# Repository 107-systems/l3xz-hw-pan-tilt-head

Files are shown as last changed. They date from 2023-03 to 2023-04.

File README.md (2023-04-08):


`l3xz-hw-pan-tilt-head`
=======================


This repository contains the design files for [L3X-Z](https://github.com/107-systems/l3xz)'s pan/tilt color/thermal camera head.

The necessary [ROS](https://docs.ros.org/en/humble/Releases.html)-based driver software for installation on the Raspberry Pi Zero can be found [here](https://github.com/107-systems/l3xz-sw-pan-tilt-head).

<p align="center">
  
</p>

## Overview
_(note that pngs with labels have draw.io diagrams embedded in them and can be edited using draw.io)_

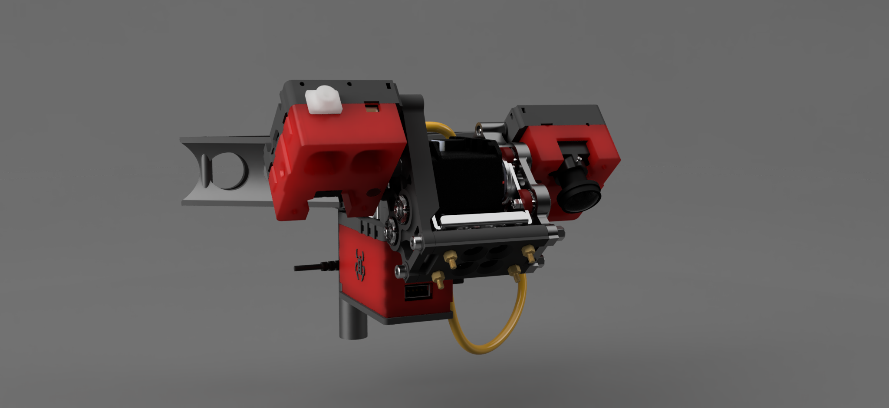
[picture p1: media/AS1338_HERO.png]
00 main LEFT


### Left View / Starboard Side
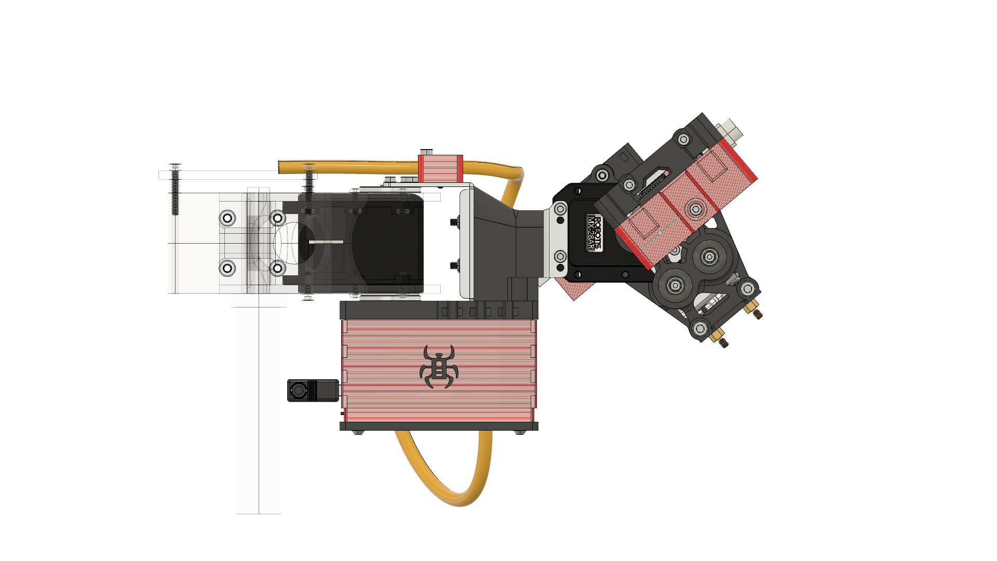
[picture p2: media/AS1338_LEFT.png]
AS1338 LEFT


### Front View
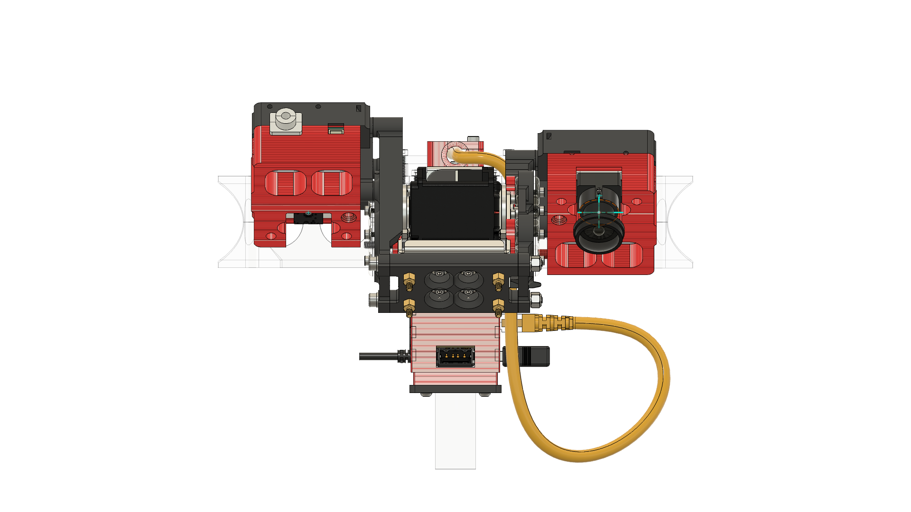
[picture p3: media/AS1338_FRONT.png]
AS1338 FRONT


### Right View / Port Side
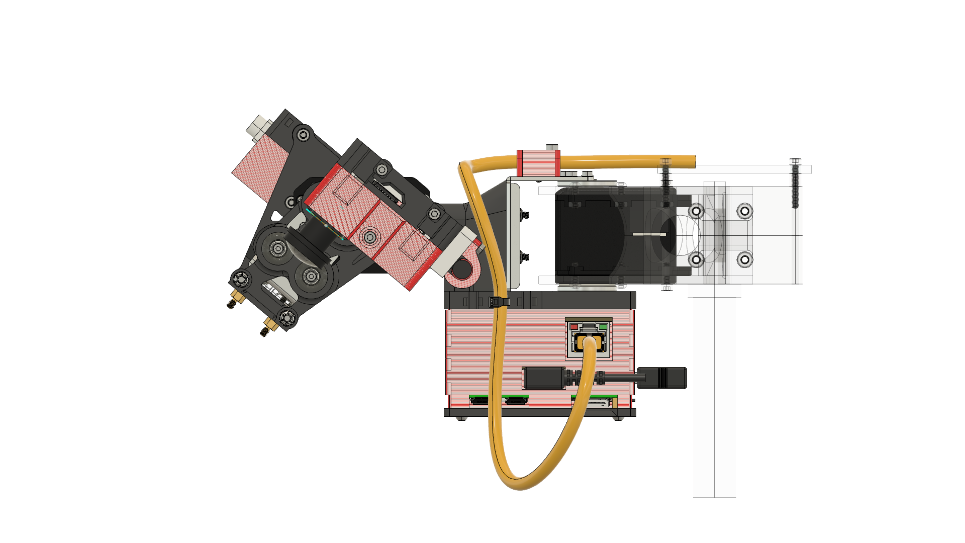
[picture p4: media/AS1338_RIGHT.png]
AS1338 RIGHT
 

### Top View
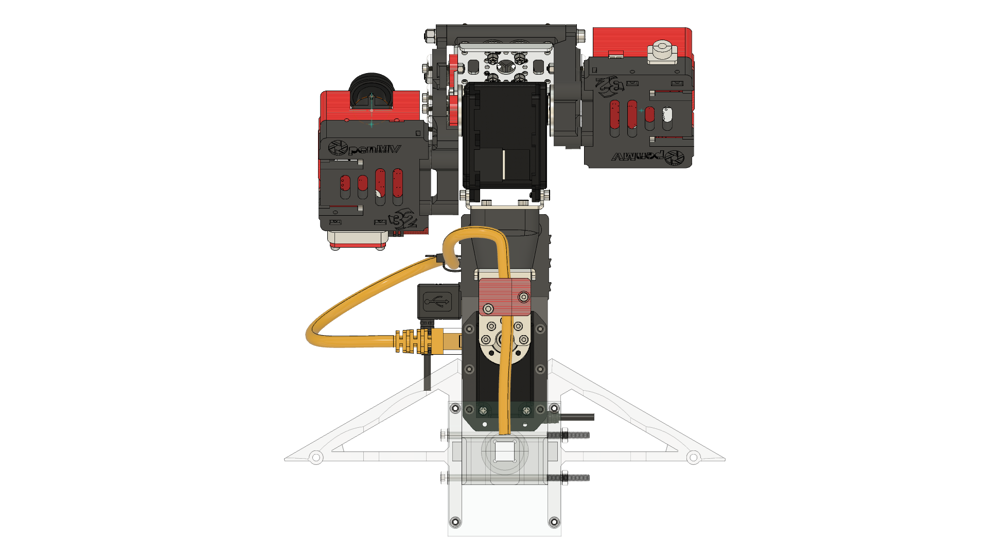
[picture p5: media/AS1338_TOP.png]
AS1338 TOP


### Bottom View
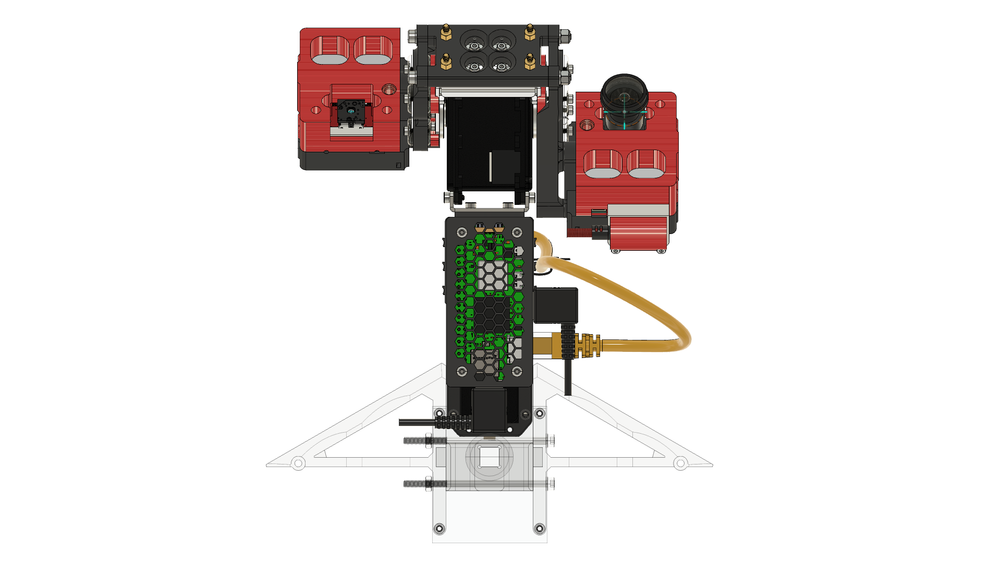
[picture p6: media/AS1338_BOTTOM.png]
AS1338 BOTTOM


### Rear View
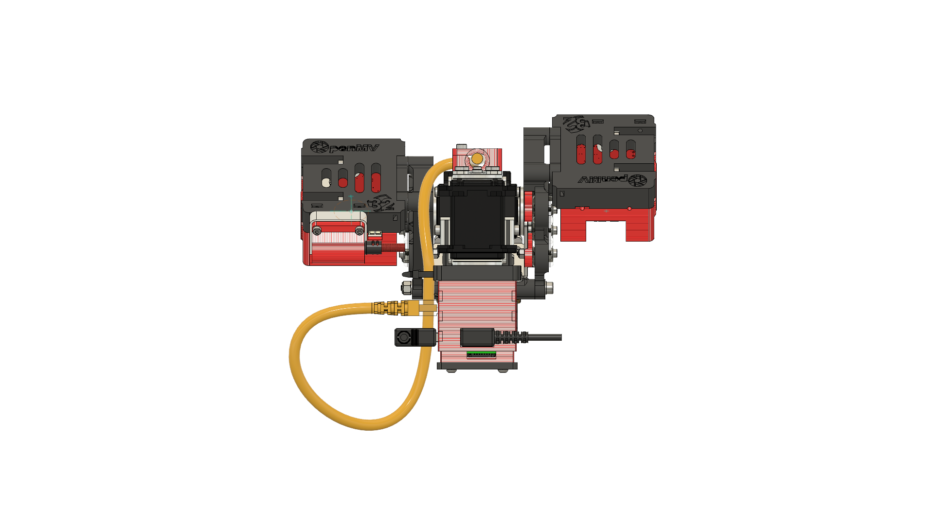
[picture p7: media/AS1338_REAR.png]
AS1338 REAR
 

### Vibration Isolation Mount Detail
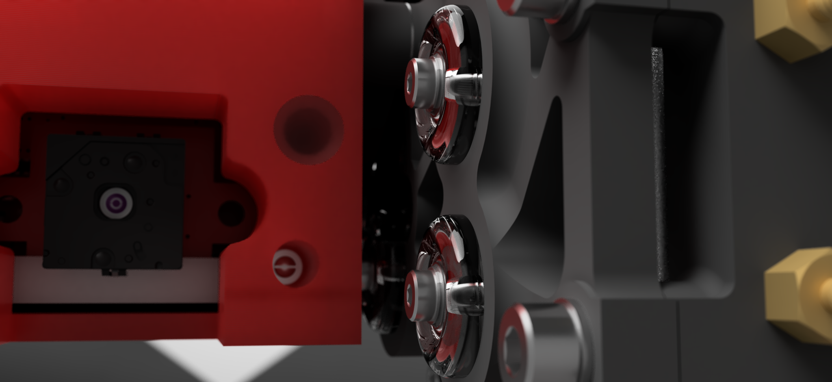
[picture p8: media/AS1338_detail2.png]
AS1338 detail 2
 

### Motion Study
[AS1338 motion study](./media/AS1338_MOTION.mp4) 

## Bill of Materials

### Raw Materials (RM)

| Part Number | Manufacturer | Mgf. Part No. | Description | SDS | TDS | Link
|---|---|---|---|-----|-----|---|
| RM0546 | hatchbox | 3D PETG-1KG1.75-RED  | Red 1.75mm PETG Filament  | | | [hatchbox3d.com](https://www.hatchbox3d.com/collections/petg-1-75mm/products/3d-petg-1kg1-75-red ) |
| RM0054 | Prusa3d | Prusament PC Blend Carbon Fiber Black 800g | Black 1.75mm Polycarbonate Filament | | |[prusa3d.com](https://www.prusa3d.com/product/prusament-pc-blend-carbon-fiber-black-800g-2/) |
| RM0543 | FilaFlex | FilaFlexible40 | White 1.75mm Flex Filament, Shore D40 | | | [prusa3d.com](https://www.prusa3d.com/product/filatech-filaflexible40-natural-white-filament-500g/) |
| RM0126 | Prusa3d | prusament-pvb-natural-transparent-500g | Transparent 1.75mm PVB Filament | | | [prusa3d.com](https://www.prusa3d.com/product/prusament-pvb-natural-transparent-500g/)|
| RM0675 | Permabond | Permabond 240 | Instant Bond Adhesive | [✓](./datasheets/sds/1570600%20GHS%20240%20021318.pdf)| [✓](./datasheets/tds/240_TDS.pdf) |[mcmaster.com](https://www.mcmaster.com/7580A85/) |
| RM0714 | 3M | DP100 | 3M™ Scotch-Weld™ Epoxy Adhesive DP100 | [✓](./datasheets/tds/DP100.pdf) | [✓](./datasheets/sds/DP100.pdf) | [amazon](https://www.amazon.com/gp/product/B07G561G2C) |
| RM0672 | 3M | DP8005 | 3M™ Scotch-Weld™ Epoxy Adhesive DP8005 | [✓](./datasheets/tds/DP8005.pdf) | [✓](./datasheets/sds/DP8005.pdf) | [amazon](https://www.amazon.com/gp/product/B007IATIK8) |
| RM0879 | (generic) | B07XFMPQR1 | 304 Stainless Steel Woven Wire 120 Mesh Fine Screen | | | [amazon](https://www.amazon.com/gp/product/B07XFMPQR1) |
| RM0889 | 3M | AC79 | 3M Scotch-Weld Instant Adhesive Primer | [✓](./datasheets/sds/AC79.pdf) | [✓](./datasheets/tds/AC79.pdf) | [amazon](https://www.amazon.com/gp/product/B071W9H889) |
| RM0890 | Loctite | Threadlocker Blue 242 | Removable thread locker to prevent self-loosening | [✓](./datasheets/sds/loctite_blue.pdf) | [✓](./datasheets/tds/loctite_blue.pdf) | [loctite](https://www.loctiteproducts.com/en/products/specialty-products/specialty/loctite_threadlockerblue242.html) |
| RM0318 | Eclectic | E6000 | Flexible, clear adhesive | | [✓](./datasheets/tds/tds-e6000-craft-us-ca-me-au-nz-mex.pdf) | [eclectic](https://eclecticproducts.com/product/e6000-industrial-adhesive/)|

### Custom FFF Parts (CF)

* Unless otherwise specified, all gcode was generated from step files using PrusaSlicer 2.6.0-alpha3+MacOS-x64
* Unless otherwise specified, all gcode was generated for a Prusa Mini+
* Unless otherwise specified, all gcode was generated for a 0.40 mm nozzle.

<table>
<thead>
<th>
    <strong>Material ID</strong><br/>
    &gt;&nbsp;Filament Profile
</th>
<th>Count</th>
<th>Part Number</th>
<th>Thumbnail</th>
<th>Description</th>
<th>Step File</th>
<th>GCode File</th>
<th>Layer Height</th>
<th>Printing Notes</th>
</thead>
<tbody valign="top">
<tr>
<td rowspan="10">
    <strong>RM0546</strong><br/>
    &gt;&nbsp;Generic PETG
</td>
<td>1</td>
<td>CF0531</td>
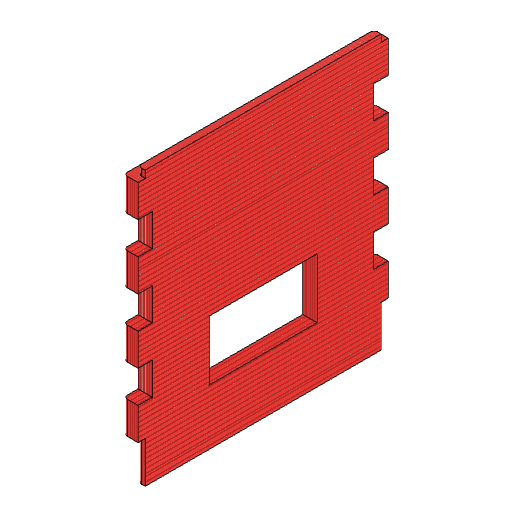
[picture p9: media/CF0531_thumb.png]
<td></td>
<td>Dragon Beard dust guard: front plate</td>
<td><a href="./models/02_parts_custom/process_fff/dragon_beard_dust_cover_front.step">✓</a></td>
<td rowspan="4"><a href="./gcode/dragon_beard_dustcover_0.15mm_PETG_MINI_1h24m.gcode">✓</a></td>
<td rowspan="10">0.15</td>
<td rowspan="8">
<ul>
    <li>Infill: Rectilinear 100%</li>
    <li>No supports</li>
    <li>powder-coated sheet w/ glue-stick</li>
    <li>no-enclosure</li>
</ul>
</td>
</tr>
<tr>
<td>1</td>
<td>CF0532</td>
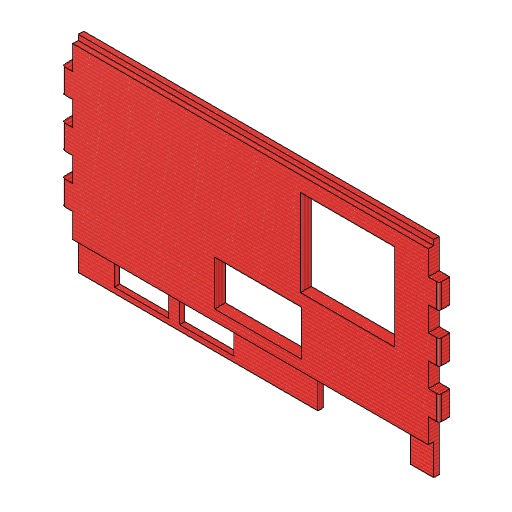
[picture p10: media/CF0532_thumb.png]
<td></td>
<td>Dragon Beard dust guard: side plate, port</td>
<td><a href="./models/02_parts_custom/process_fff/dragon_beard_dust_cover_port.step">✓</a></td>
</tr>
<tr>
<td>1</td>
<td>CF0533</td>
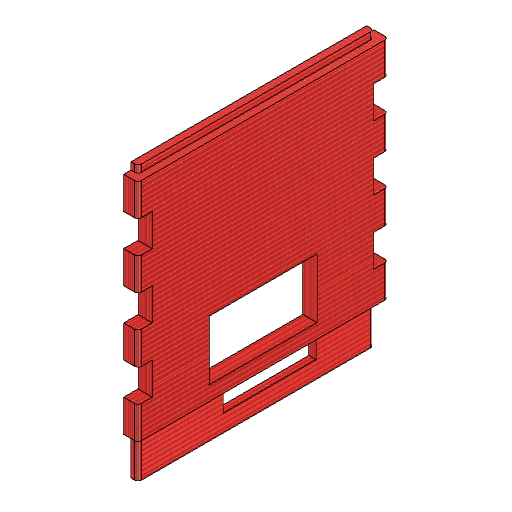
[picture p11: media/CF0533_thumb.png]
<td></td>
<td>Dragon Beard dust guard: rear plate</td>
<td><a href="./models/02_parts_custom/process_fff/dragon_beard_dust_cover_rear.step">✓</a></td>
</tr>
<tr>
<td>1</td>
<td>CF0534</td>
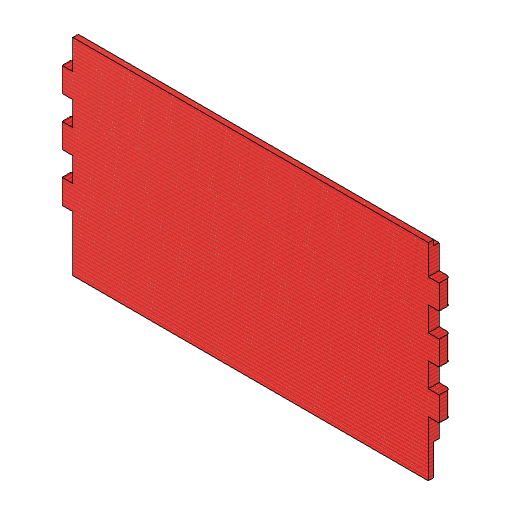
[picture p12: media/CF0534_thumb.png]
<td></td>
<td>Dragon Beard dust guard: side plate, starboard</td>
<td><a href="./models/02_parts_custom/process_fff/dragon_beard_dust_cover_starboard.step">✓</a></td>
</tr>
</tr>
<tr>
<td>1</td>
<td>CF0535</td>
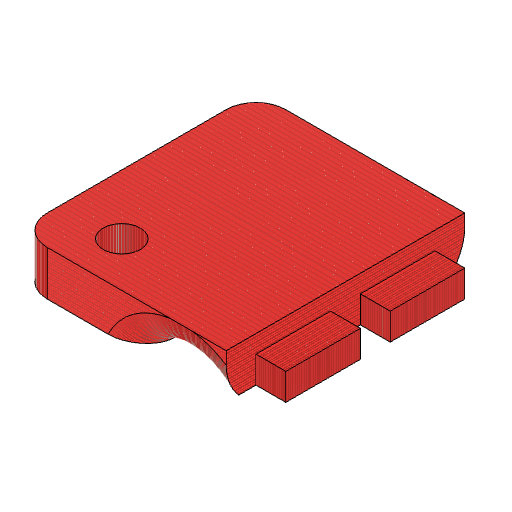
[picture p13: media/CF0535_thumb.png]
<td></td>
<td>Ethernet Cable Guide, top</td>
<td><a href="./models/02_parts_custom/process_fff/dragon_neck_ethernet_guide_top.step">✓</a></td>
<td rowspan="2"><a href="./gcode/Ethernet_guide_0.15mm_PETG_MINI_59m.gcode">✓</a></td>
</tr>
<tr>
<td>1</td>
<td>CF0536</td>
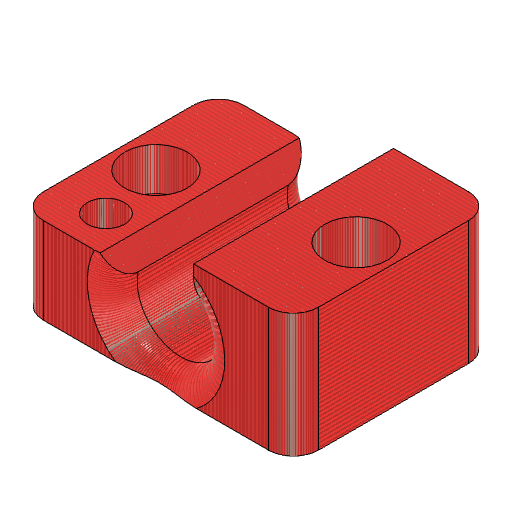
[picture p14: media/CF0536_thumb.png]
<td></td>
<td>Ethernet Cable Guide, bottom</td>
<td><a href="./models/02_parts_custom/process_fff/dragon_neck_ethernet_guide_bottom.step">✓</a></td>
</tr>
<tr>
<td>2</td>
<td>CF0538</td>
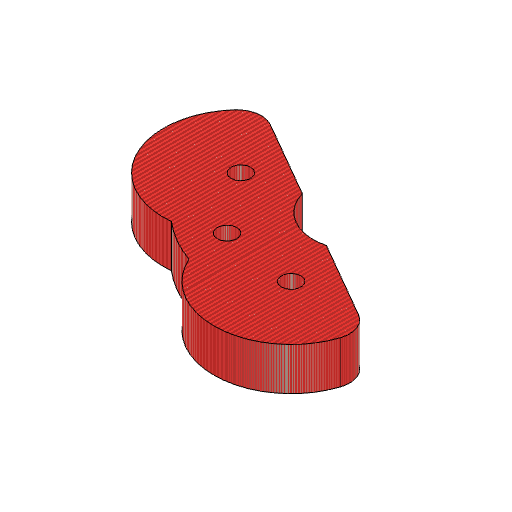
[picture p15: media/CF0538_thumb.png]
<td></td>
<td>Axial Squash Plate</td>
<td><a href="./models/02_parts_custom/process_fff/dragon_eye_squashplate_axial.step">✓</a></td>
<td rowspan="2"><a href="./gcode/squash_plates_0.15mm_PETG_MINI_27m.gcode">✓</a></td>
</tr>
<tr>
<td>4</td>
<td>CF0539</td>
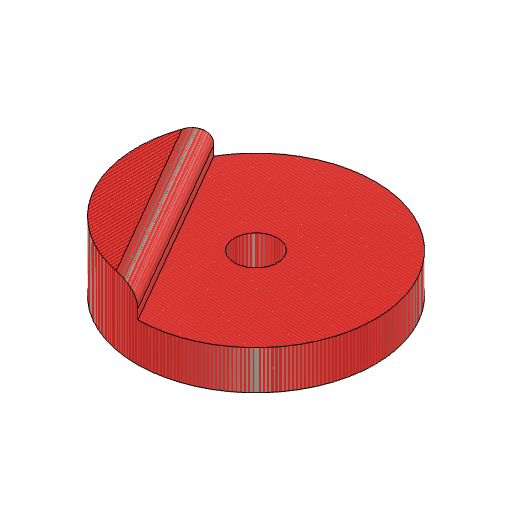
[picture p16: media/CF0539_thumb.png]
<td></td>
<td>Distal Squash Plate</td>
<td><a href="./models/02_parts_custom/process_fff/dragon_eye_squashplate.step">✓</a></td>
</tr>
<tr>
<td>2</td>
<td>CF0537</td>
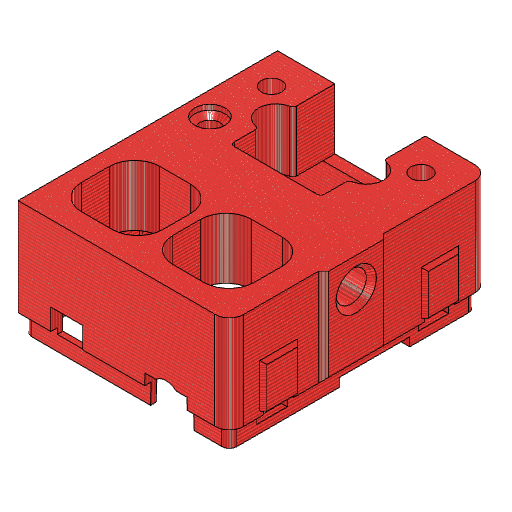
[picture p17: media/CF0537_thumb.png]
<td></td>
<td>OpenMV H7 Case, Front</td>
<td><a href="./models/02_parts_custom/process_fff/omvh732_front.step">✓</a></td>
<td><a href="./gcode/omvh732_front_0.15mm_PETG_MINI_2h7m.gcode">✓</a></td>
<td>
<ul>
    <li>Infill: Gyroid 20%</li>
    <li>Solid infill threshold area: 200mm<sup>2</sup></li>
    <li>No supports</li>
    <li>powder-coated sheet w/ glue-stick</li>
    <li>no-enclosure</li>
</ul>
</td>
</tr>
<tr>
<td>2</td>
<td>CF0562</td>
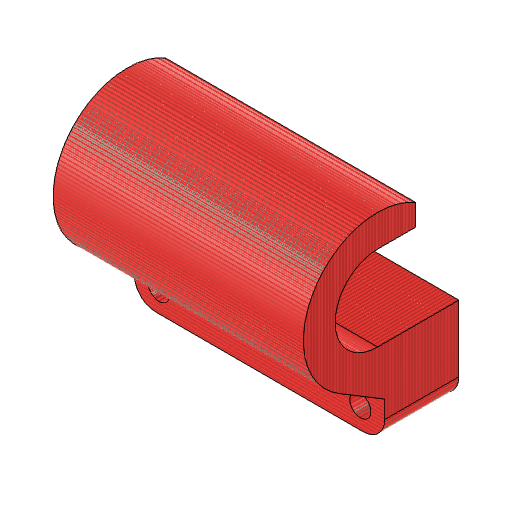
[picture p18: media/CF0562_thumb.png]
<td></td>
<td>OpenMV H7 Case, USB Retainer</td>
<td></td>
<td><a href="./gcode/omvh732_usb_retainer_0.15mm_PETG_MINI_39m.gcode">✓</a></td>
<td>
<ul>
    <li>Infill: Rectilinear 100%</li>
    <li>Custom Support</li>
    <li>Support Style: Snug</li>
    <li>powder-coated sheet w/ glue-stick</li>
    <li>no-enclosure</li>
</ul>
</td>
</tr>
<tr>
<td rowspan="6">
    <strong>RM0543</strong><br/>
    &gt;&nbsp;Filatech FilaFlex40
</td>
<td>2</td>
<td>CF0540</td>
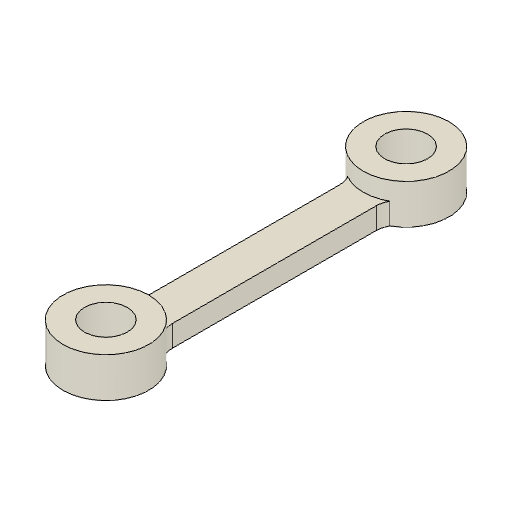
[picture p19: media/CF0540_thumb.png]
<td></td>
<td>OpenMV H7 Case, soft-mount, rear.</td>
<td><a href="./models/02_parts_custom/process_fff/omvh732_softmount_rear.step">✓</a></td>
<td rowspan="4"><a href="./gcode/omvh732_softparts_0.2mm_FLEX_MINI_34m.gcode">✓</a></td>
<td rowspan="7">0.20</td>
<td rowspan="7">
<ul>
    <li>Infill: Rectilinear 100%</li>
    <li>No supports</li>
    <li>brim</li>
    <li>powder-coated sheet w/ glue-stick</li>
    <li>no-enclosure</li>
</ul>
</td>
</tr>
<tr>
<td>2</td>
<td>CF0541</td>
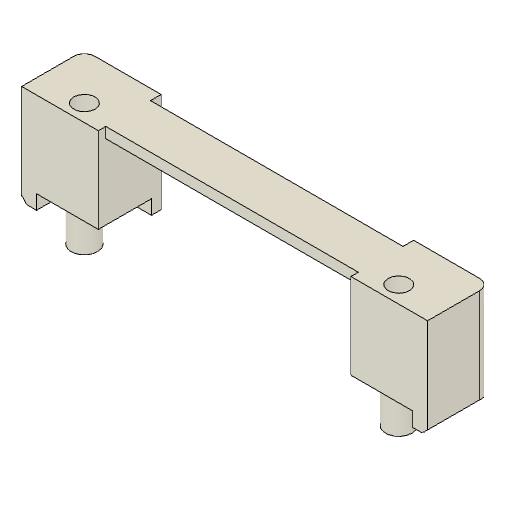
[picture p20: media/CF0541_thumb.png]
<td></td>
<td>OpenMV H7 Case, soft-mount, front-top.</td>
<td><a href="./models/02_parts_custom/process_fff/omhv732_softmount_front_top.step">✓</a></td>
</tr>
<tr>
<td>2</td>
<td>CF0542</td>
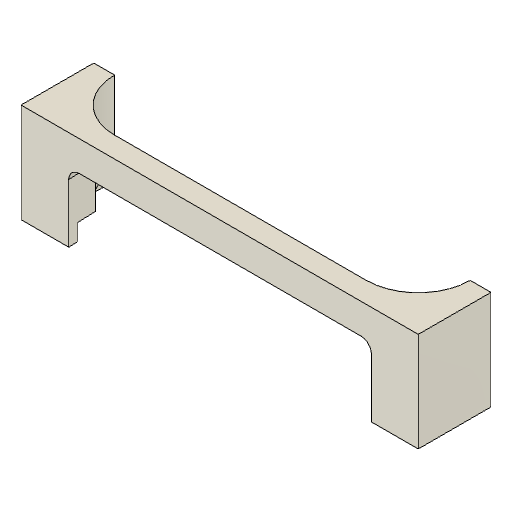
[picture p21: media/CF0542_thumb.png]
<td></td>
<td>OpenMV H7 Case, soft-mount, front-bottom.</td>
<td><a href="./models/02_parts_custom/process_fff/omhv732_softmount_front_bottom.step">✓</a></td>
</tr>
<tr>
<td>4</td>
<td>CF0543</td>
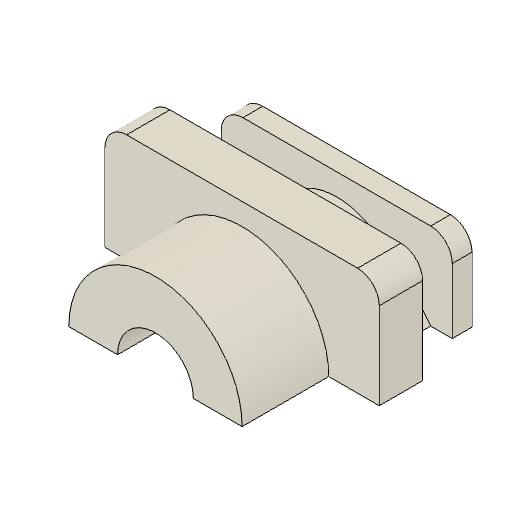
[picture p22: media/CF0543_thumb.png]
<td></td>
<td>OpenMV H7 Case, no-connector strain-relief.</td>
<td><a href="./models/02_parts_custom/process_fff/openmv-h7-body-strain-relief.step">✓</a></td>
</tr>
<tr>
<td>1</td>
<td>CF0580</td>
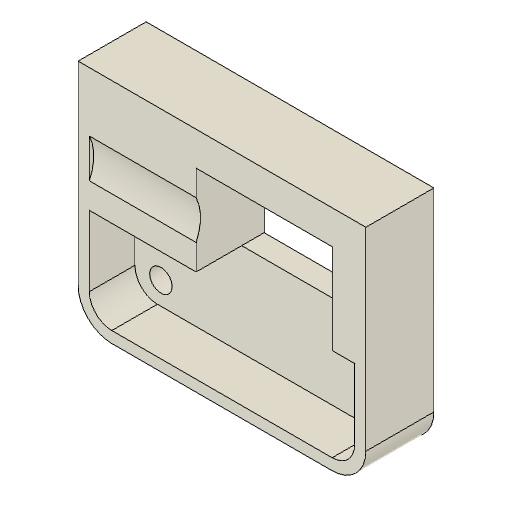
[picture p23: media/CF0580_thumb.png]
<td></td>
<td>OpenMV H7 Case, AAOTOKK USB Micro Retainer Gasket.</td>
<td><a href="./models/02_parts_custom/process_fff/omvh732_usb_retainer_gasket.step">✓</a></td>
<td><a href="./gcode/d.15mm_FLEX_MINI_20m.gcode">✓</a></td>
</tr>
<tr>
<td>7</td>
<td>CF0581</td>
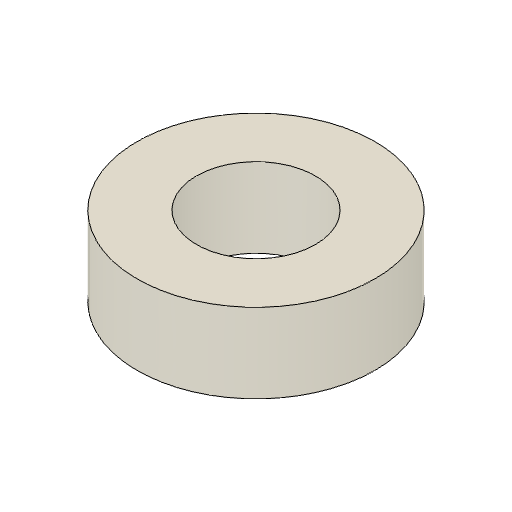
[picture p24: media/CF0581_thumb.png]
<td></td>
<td>Dragon Ear ISO mount spacers</td>
<td><a href="models/02_parts_custom/process_fff/dragon_ear_iso_spacer.step">✓</a></td>
<td><a href="./gcode/iso_spacer_0.2mm_FLEX_MINI_7m.gcode">✓</a></td>
</tr>
<tr>
<td>
    <strong>RM0126</strong><br/>
    &gt; Prusament PVB
</td>
<td>2</td>
<td>CF0544</td>
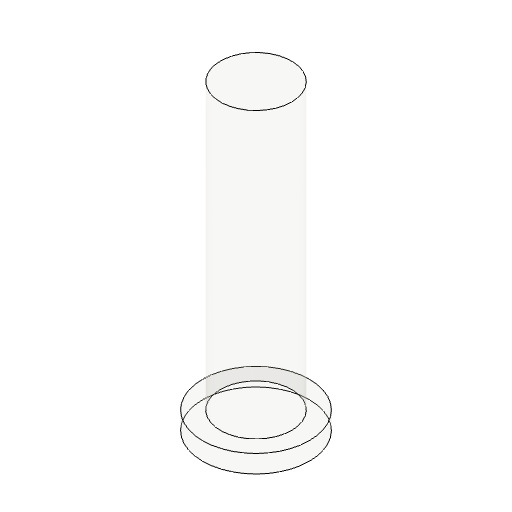
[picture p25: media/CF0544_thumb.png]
<td></td>
<td>OpenMV H7 Case, light-pipe.</td>
<td><a href="./models/02_parts_custom/process_fff/omhv732_lightpipe_front.step">✓</a></td>
<td><a href="./gcode/omvh732_lightpipe_0.2mm_PVB_MINI_5m.gcode">✓</a></td>
</tr>
<tr>
<td rowspan="10">
    <strong>RM0054</strong><br/>
    &gt;&nbsp;Prusament&nbsp;PC&nbsp;Blend&nbsp;Carbon&nbsp;Fiber&nbsp;+
    <ul>
    <li>extrusion mult. .97</li>
    <li>nozzle temp: 290˚ (all layers)</li>
    <li>enclosure, 32˚</li>
    </ul>
</td>
<td>1</td>
<td>CF0545</td>
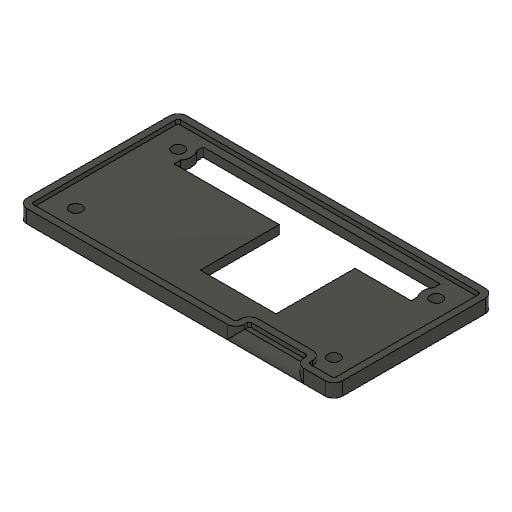
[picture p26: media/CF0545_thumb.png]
<td></td>
<td>Dragon Beard boot: design variant 1</td>
<td><a href="./models/02_parts_custom/process_fff/dragon_beard_boot_d1.step">✓</a></td>
<td><a href="./gcode/boot_d1_0.15mm_PC_MINI_39m.gcode">✓</a></td>
<td rowspan="8">0.15</td>
<td rowspan="4">
<ul>
    <li>Infill: Rectilinear 100%</li>
    <li>No supports</li>
    <li>powder-coated sheet</li>
</ul>
</td>
</tr>
<tr>
<td>1</td>
<td>CF0546</td>
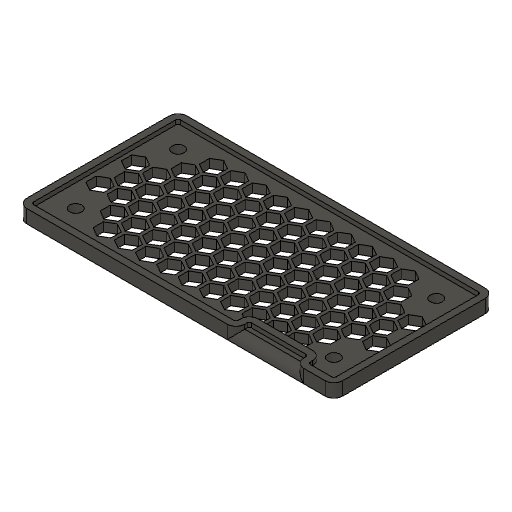
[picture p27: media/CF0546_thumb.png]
<td></td>
<td>Dragon Beard boot: design variant_2</td>
<td><a href="./models/02_parts_custom/process_fff/dragon_beard_boot_d2.step">✓</a></td>
<td><a href="./gcode/boot_d2_0.15mm_PC_MINI_39m.gcode">✓</a></td>
</tr>
<tr>
<td>1</td>
<td>CF0547</td>
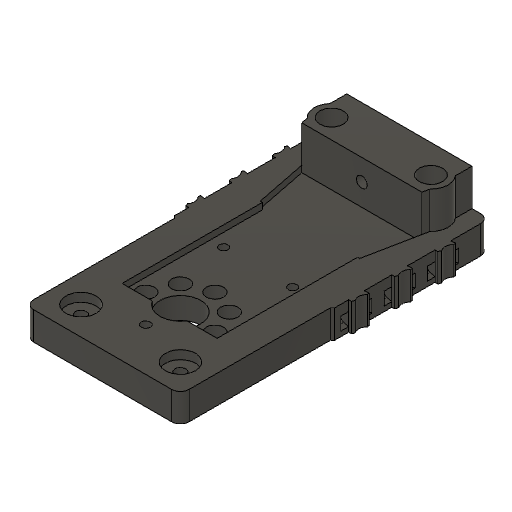
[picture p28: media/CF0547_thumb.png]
<td></td>
<td>Dragon Beard hanger</td>
<td><a href="./models/02_parts_custom/process_fff/dragon_beard_hanger.step">✓</a></td>
<td><a href="./gcode/hanger_0.15mm_PC_MINI_2h8m.gcode">✓</a></td>
</tr>
<tr>
<td>1</td>
<td>CF0548</td>
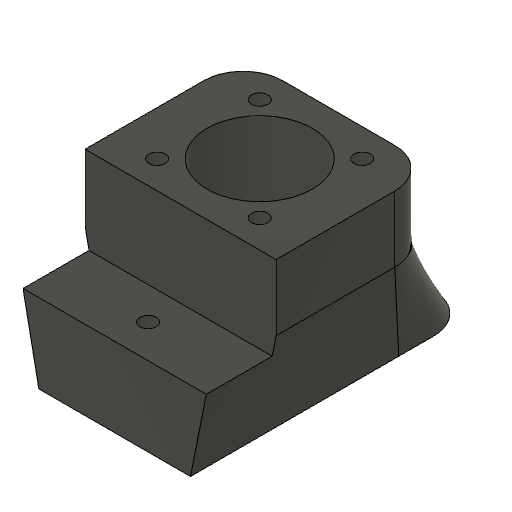
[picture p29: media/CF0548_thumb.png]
<td></td>
<td>Dragon Beard neck (25mm)</td>
<td><a href="./models/02_parts_custom/process_fff/dragon_neck_25mm.step">✓</a></td>
<td><a href="./gcode/neck_25mm_0.15mm_PC_MINI_2h9m.gcode">✓</a></td>
</tr>
<tr>
<td>1</td>
<td>CF0549</td>
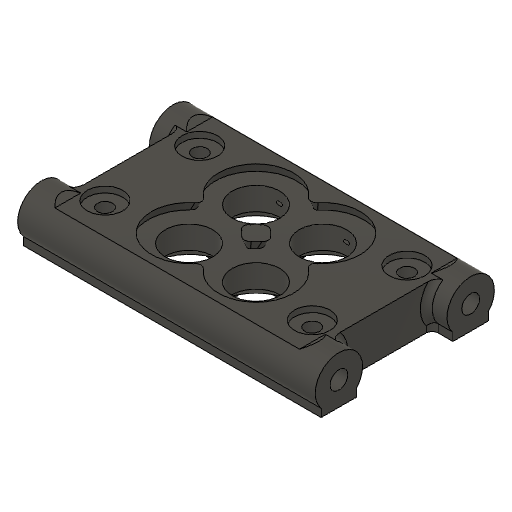
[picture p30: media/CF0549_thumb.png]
<td></td>
<td>Dragon Nose</td>
<td><a href="./models/02_parts_custom/process_fff/dragon_nose.step">✓</a></td>
<td><a href="./gcode/nose_0.15mm_PC_MINI_1h9m.gcode">✓</a></td>
<td rowspan="2">
<ul>
    <li>Infill: Honeycomb 30%</li>
    <li>4 perimeters (min)</li>
    <li>Bottom layer: Archimedean Chords</li>
    <li>Custom supports</li>
    <li>Support Style: Snug</li>
    <li>powder-coated sheet</li>
</ul>
</td>
</tr>
<tr>
<td>2</td>
<td>CF0550</td>
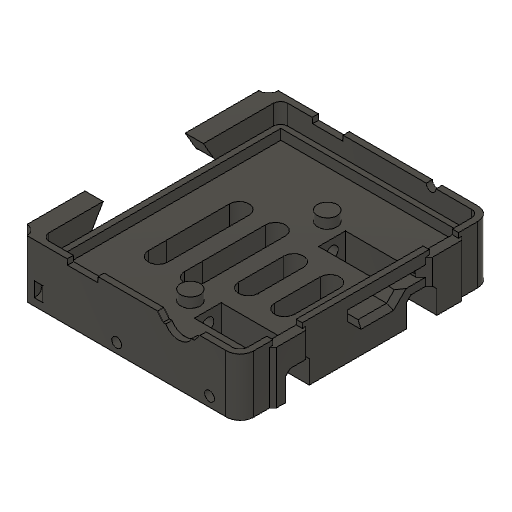
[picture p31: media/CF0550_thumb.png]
<td></td>
<td>OpenMV H7 Case: Rear</td>
<td><a href="./models/02_parts_custom/process_fff/omvh732_rear.step">✓</a></td>
<td><a href="./gcode/omvh732_rear_0.15mm_PC_MINI_1h43m.gcode">✓</a></td>
</tr>
<tr>
<td>1</td>
<td>CF0552</td>
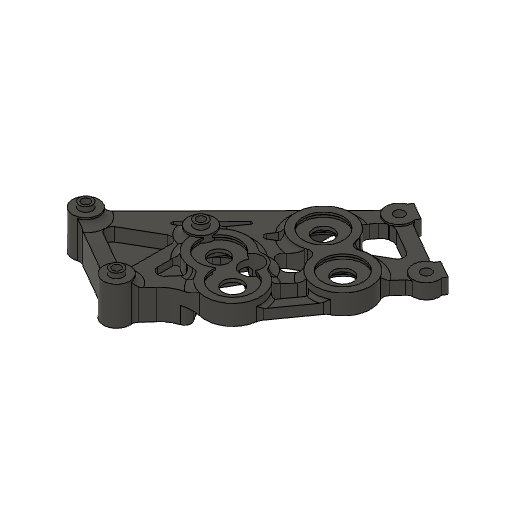
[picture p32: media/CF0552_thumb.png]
<td></td>
<td>Dragon Ear: Port-side</td>
<td><a href="./models/02_parts_custom/process_fff/dragon_ear_port.step">✓</a></td>
<td><a href="./gcode/dragon_ear_port_0.15mm_PC_MINI_2h5m.gcode">✓</a></td>
<td>
<ul>
    <li>Infill: Rectilinear 100%</li>
    <li>8 perimeters (min)</li>
    <li>Custom supports</li>
    <li>Support Style: Snug, 2mm xy separation</li>
    <li>powder-coated sheet</li>
</ul>
</td>
</tr>
<tr>
<td>2</td>
<td>CF0554</td>
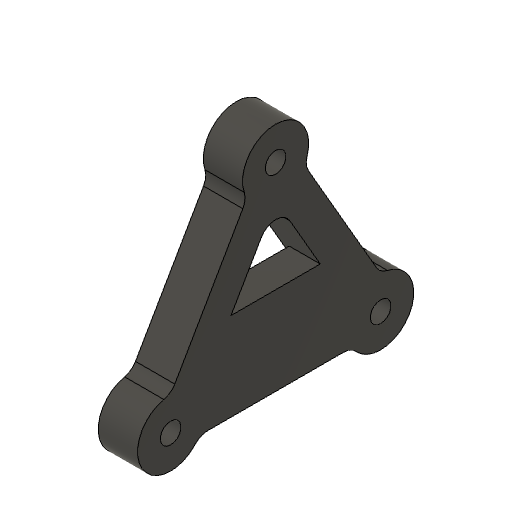
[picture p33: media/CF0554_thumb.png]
<td></td>
<td>OpenMV H7 Case: mounting adapter</td>
<td><a href="./models/02_parts_custom/process_fff/omvh732_adapter.step">✓</a></td>
<td><a href="./gcode/omv732_adapter_0.15mm_PC_MINI_39m.gcode">✓</a></td>
<td>0.10</td>
<td>
<ul>
    <li>Infill: Rectilinear 100%</li>
    <li>powder-coated sheet</li>
</ul>
</td>
</tr>
<tr>
<td>1</td>
<td>CF0551</td>
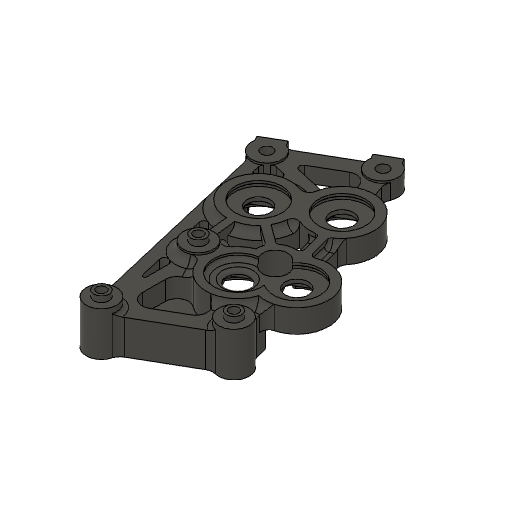
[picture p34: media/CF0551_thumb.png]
<td></td>
<td>Dragon Ear: Starboard-side</td>
<td><a href="./models/02_parts_custom/process_fff/dragon_ear_starboard.step">✓</a></td>
<td><a href="./gcode/dragon_ear_starboard_0.15mm_PC_MINI_1h54m.gcode">✓</a></td>
<td>
<ul>
    <li>Infill: Rectilinear 100%</li>
    <li>8 perimeters (min)</li>
    <li>Custom supports</li>
    <li>Support Style: Snug, 2mm xy separation</li>
    <li>powder-coated sheet</li>
</ul>
</td>
</tr>
<tr>
<td>1</td>
<td>CF0553</td>
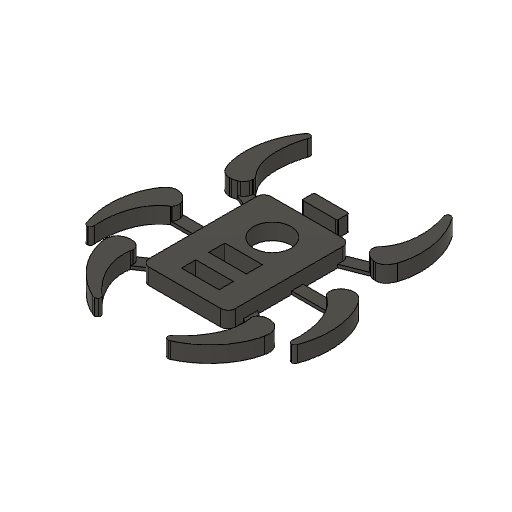
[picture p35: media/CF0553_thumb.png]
<td></td>
<td>Hexapod Emblem</td>
<td><a href="./models/00_marks_and_decals/hexapod makers mark.step">✓</a></td>
<td><a href="./gcode/hexapod_logo_0.1mm_PC_MINI_3m.gcode">✓</a></td>
<td>0.10</td>
<td>
<ul>
    <li>Infill: Rectilinear 100%</li>
    <li>powder-coated sheet</li>
</ul>
</td>
</tr>
</tbody>
</table>

### Electrical (EL)

| Ct. | Part Number | Mgfr. Part Number | Description | Link |
|-----|---|---|---|---|
| 2 | EL2112 | openmv-cam-h7-r2 | Open Machine Vision camera module. | [openmv.io](https://openmv.io/collections/cams/products/openmv-cam-h7-r2) |
| 1 | EL2113 | flir-lepton-adapter-module | OpenMV camera module adapter for FLIR lepton. | [openmv.io](https://openmv.io/collections/cams/products/flir-lepton-adapter-module)
| 1 | EL2114 | flir-lepton-3-5 | FLIR Lepton imaging module. | [groupgets.com](https://store.groupgets.com/products/flir-lepton-3-5) |
| 1 | EL2115 | Raspberry Pi Zero 2 W | SBC compute module | [raspberrypi.com](https://www.raspberrypi.com/products/raspberry-pi-zero-2-w/) |
| 1 | EL2116 | PoE/ETH/USB HUB HAT | PoE hat for EL2115 | [waveshare.com](https://www.waveshare.com/poe-eth-usb-hub-hat.htm) |
| 2 | EL2117 | 902-0095-000 | DYNAMIXEL MX-28AR servo | [robotis.com](https://www.robotis.us/dynamixel-mx-28ar/) |

### Assemblies (AS)

| Ct. | Part Number | Image | Anim. | Description |
|-----|---|---|---|---|
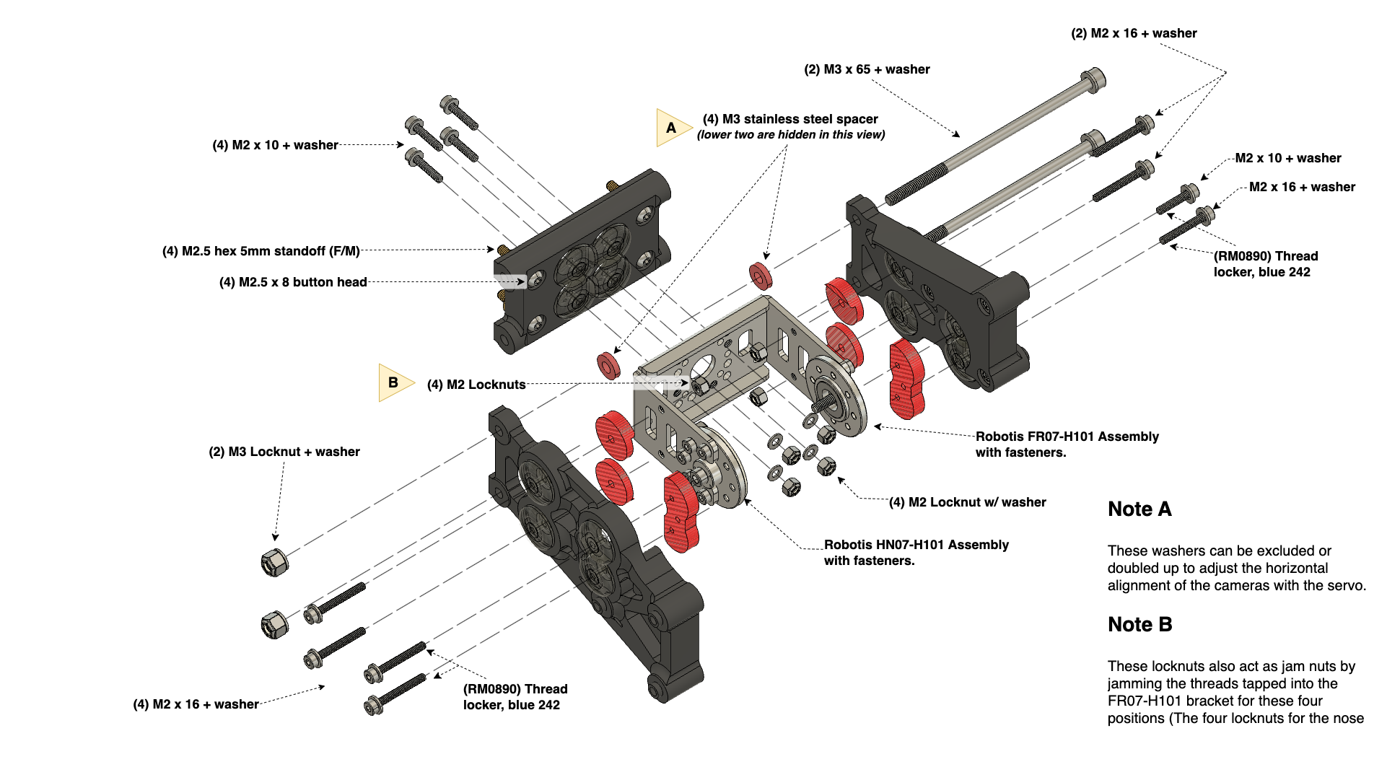
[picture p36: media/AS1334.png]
| 1 | AS1334 | [](./media/AS1334.png) | [✓](./media/AS1334.mp4) | Dragon Face|
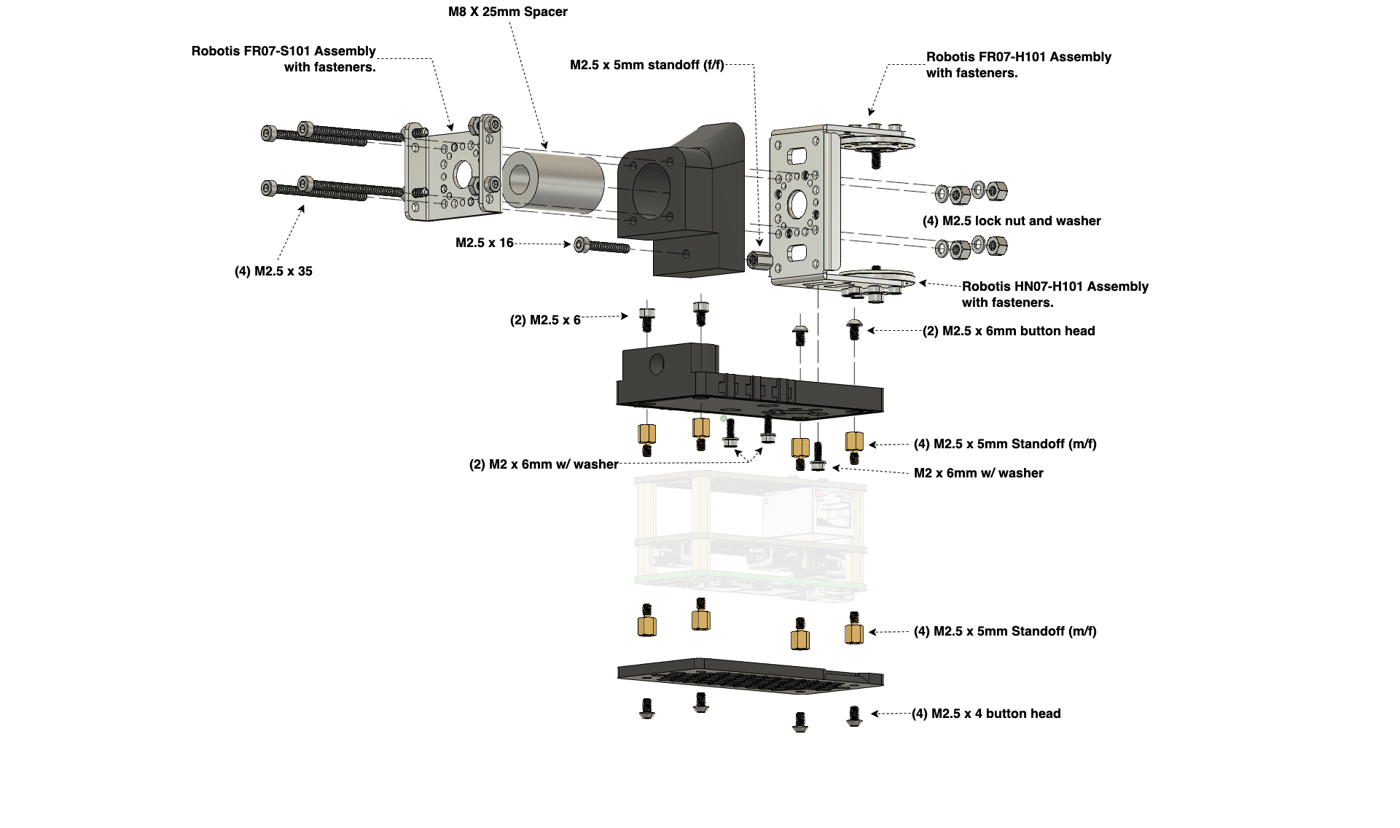
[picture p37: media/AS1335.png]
| 1 | AS1335 | [](./media/AS1335.png) | [✓](./media/AS1335.mp4) | Dragon Throat|
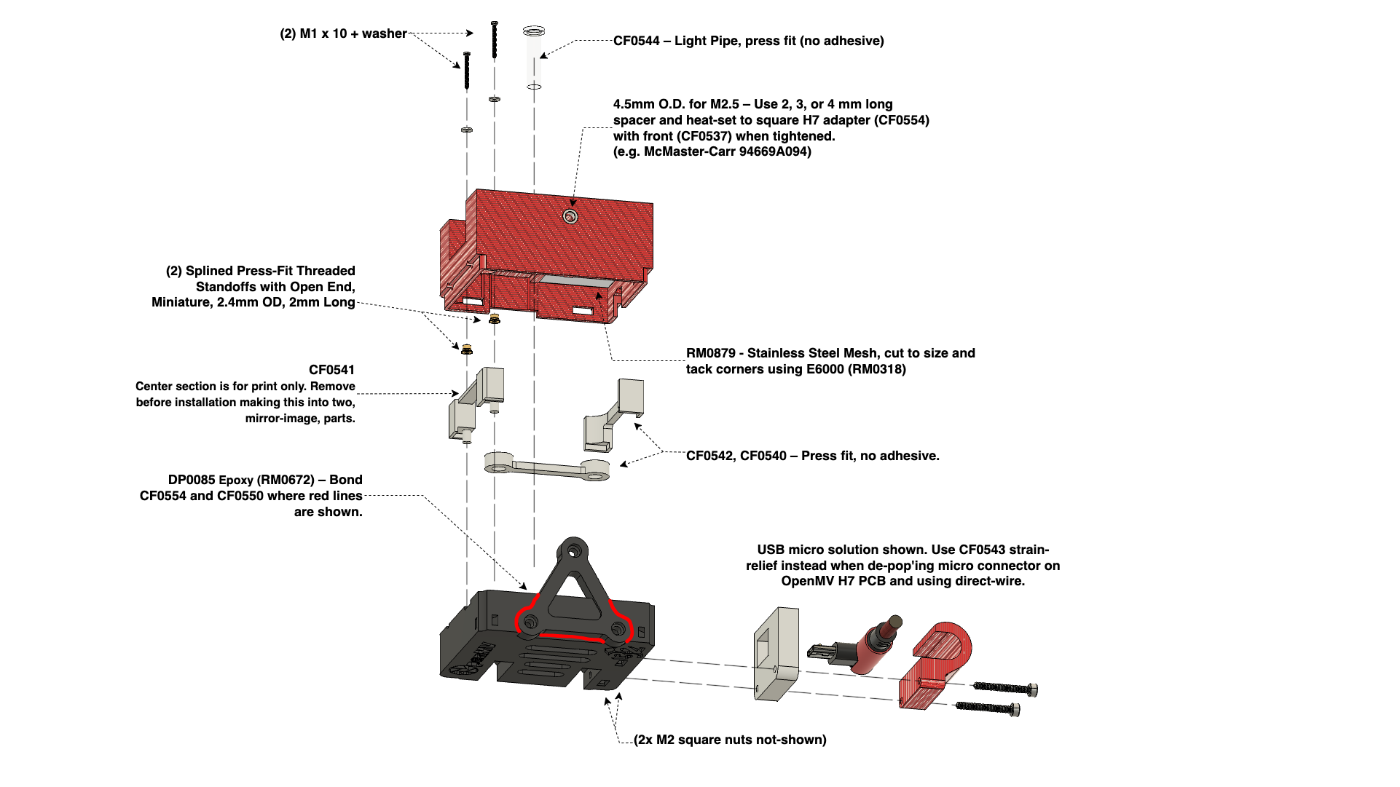
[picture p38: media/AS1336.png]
| 1 | AS1336 | [](./media/AS1336.png) | [✓](./media/AS1336.mp4) | OpenMV H7 Camera Enclosure |
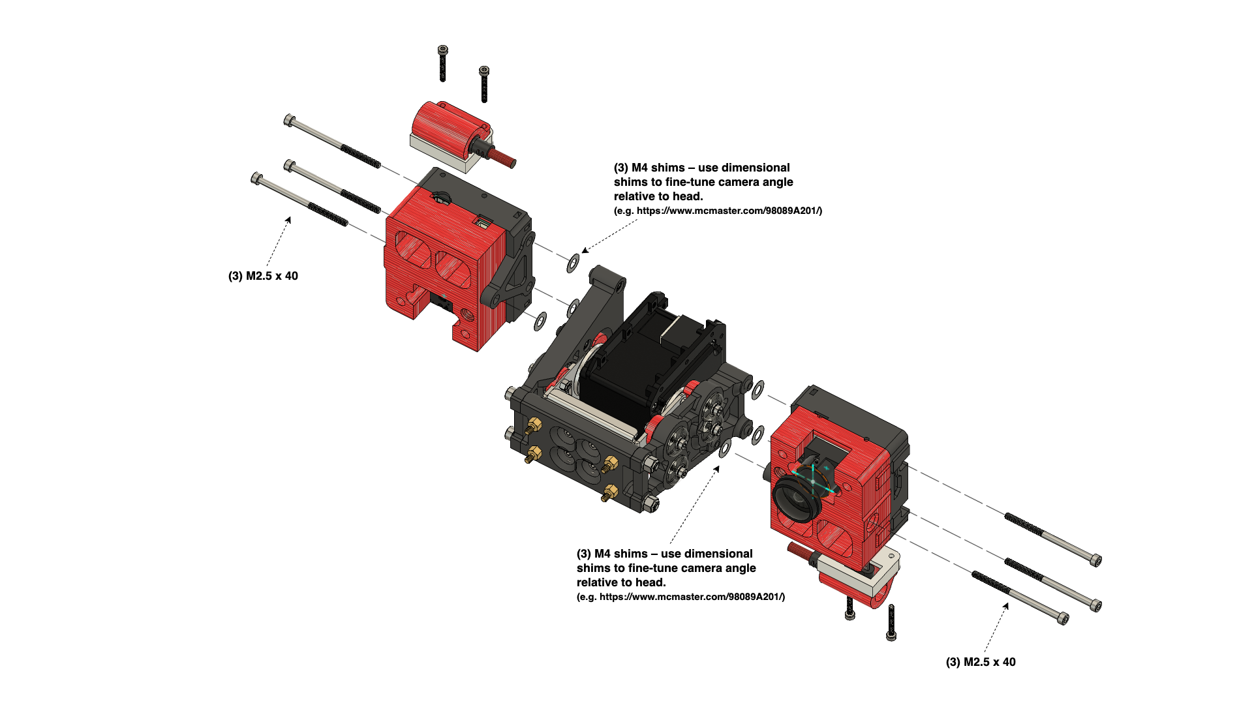
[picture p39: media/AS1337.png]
| 1 | AS1337 | [](./media/AS1337.png) | [✓](./media/AS1337.mp4) | Camera Head |
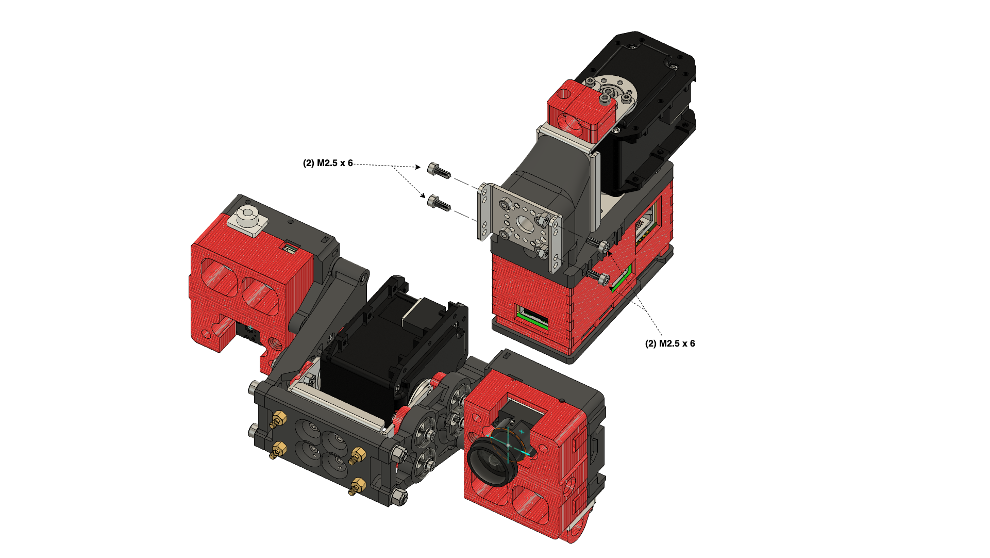
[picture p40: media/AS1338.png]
| 1 | AS1338 | [](./media/AS1338.png) | | Main Assembly |

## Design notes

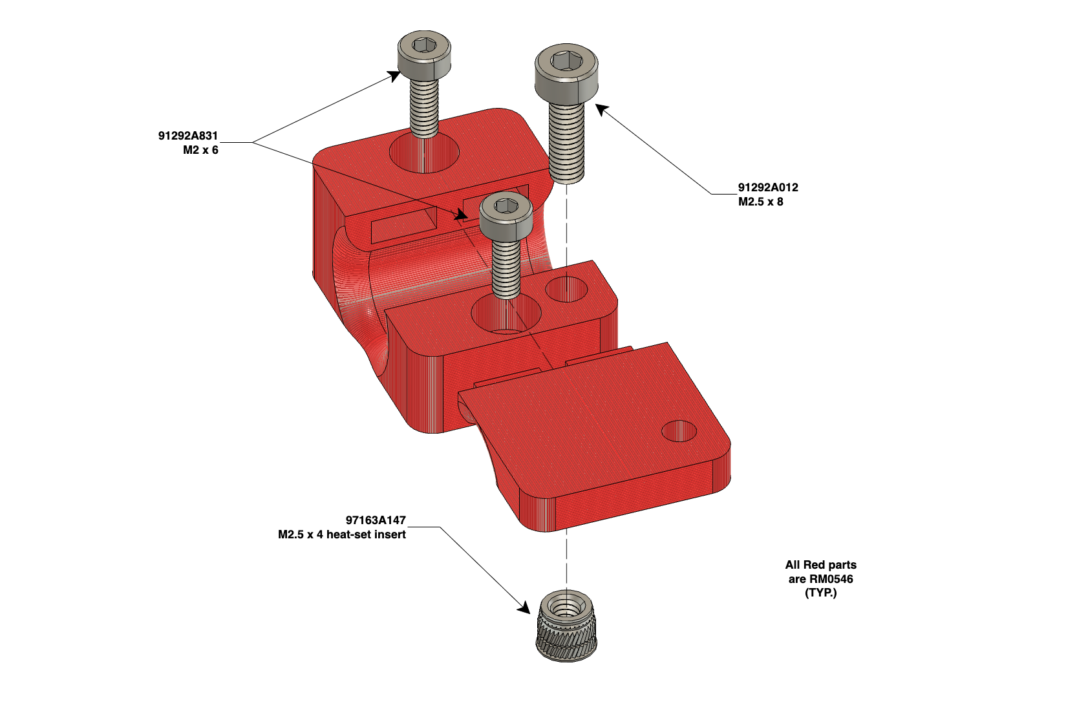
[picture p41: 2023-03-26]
media/AS1333.png

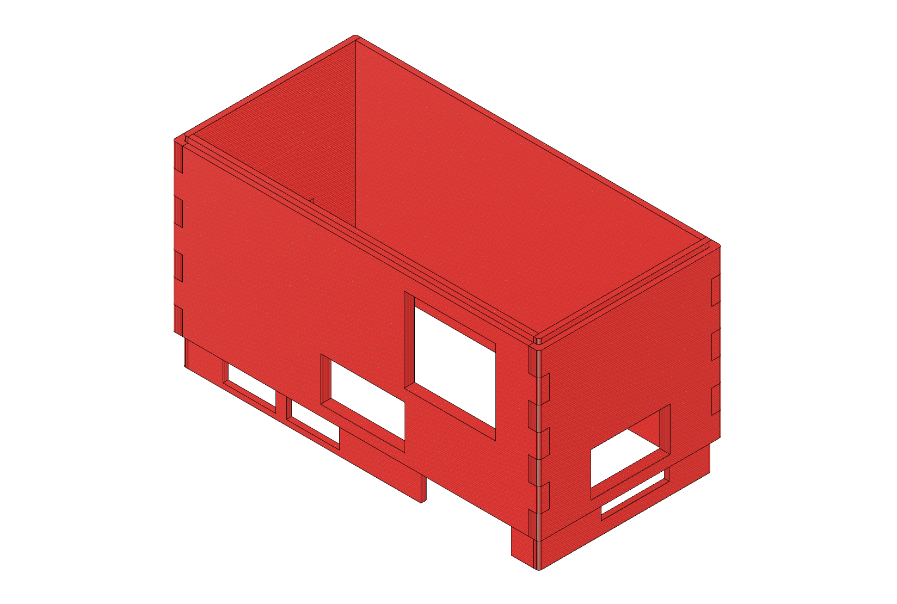
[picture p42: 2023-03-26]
media/AS1332.png

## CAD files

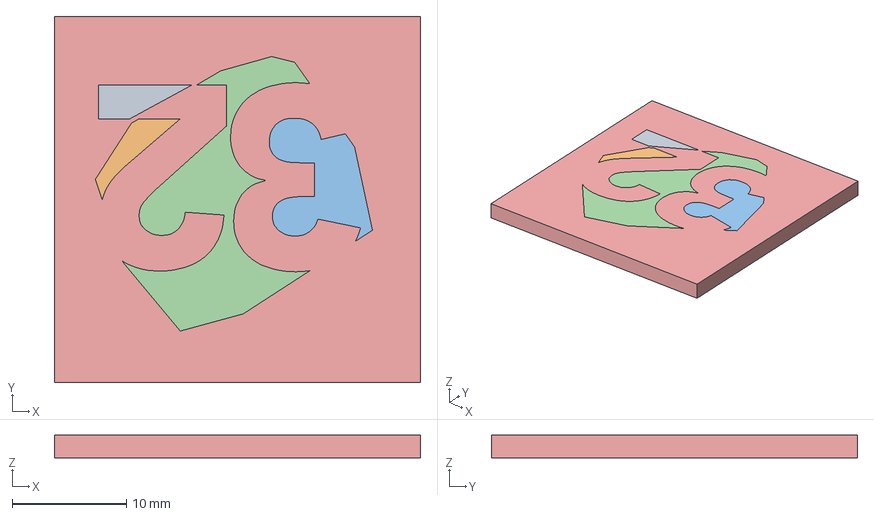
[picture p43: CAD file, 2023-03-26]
models/00_marks_and_decals/32 makers mark.step
32.0 x 32.0 x 2.00 mm

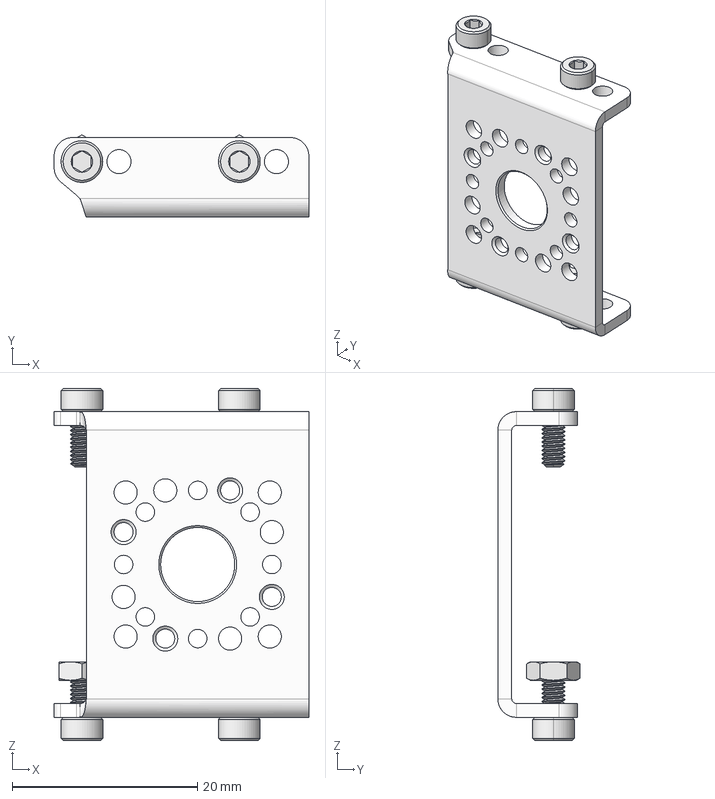
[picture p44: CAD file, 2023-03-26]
models/01_parts_stock/FR07-S101-w-fasteners.step
27.5 x 8.89 x 38.0 mm
FR07-S101 v2
91828A113_18-8 Stainless Steel Hex Nut x 2
91292A010_18-8 Stainless Steel Socket Head Screw x 4

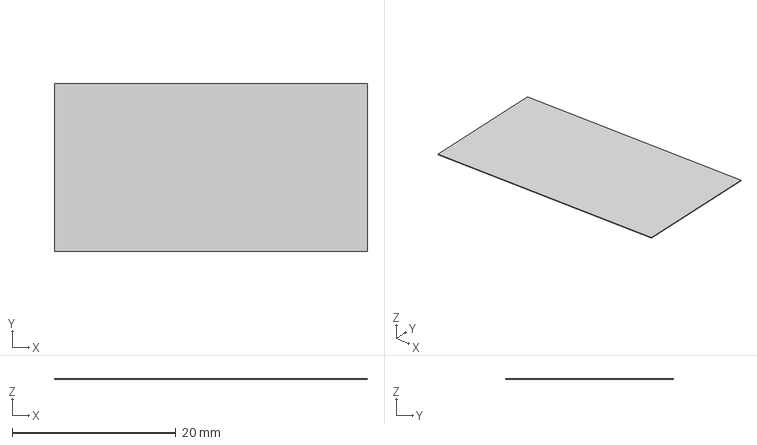
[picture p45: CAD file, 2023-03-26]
models/02_parts_custom/process_adhoc/omvh732_front_fod_filter.step
38.2 x 20.5 x 0.1 mm

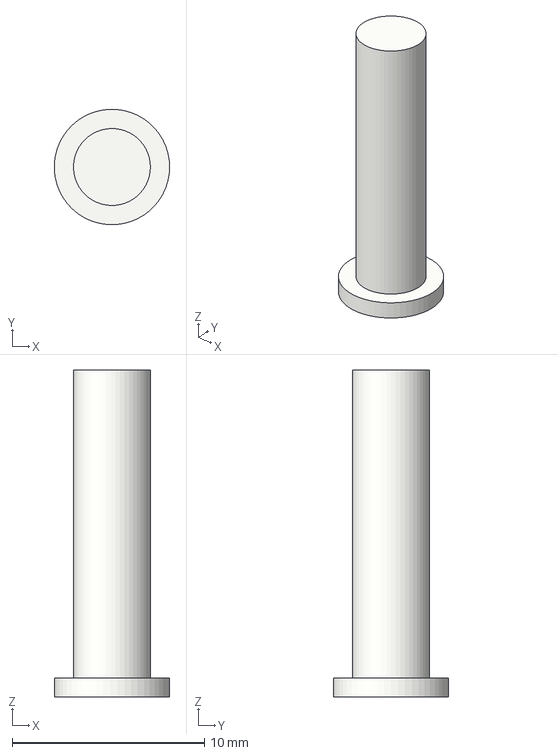
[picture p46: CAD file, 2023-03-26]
models/02_parts_custom/process_fff/omhv732_lightpipe_front.step
5.99 x 6.00 x 17.0 mm

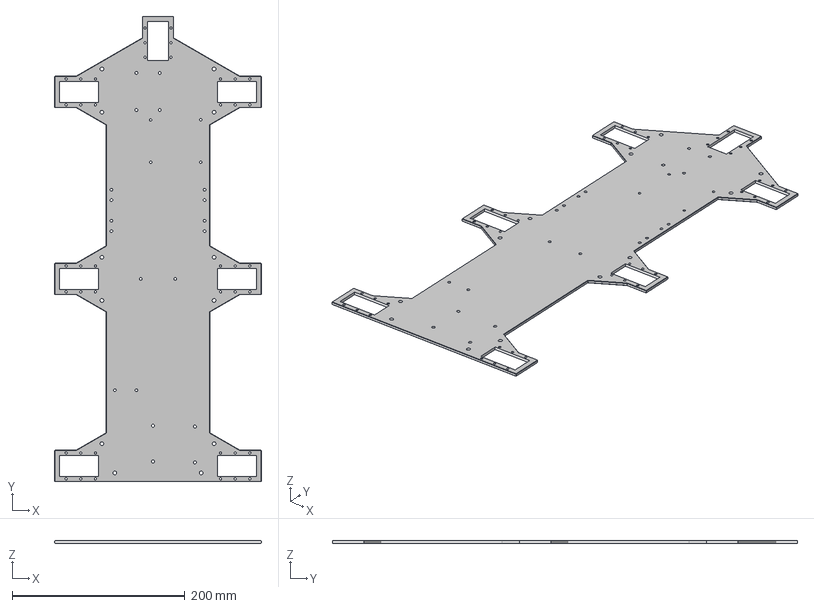
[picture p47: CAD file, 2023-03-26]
models/02_parts_custom/process_laser_cut/body-bottom.step
240.0 x 539.4 x 3.00 mm

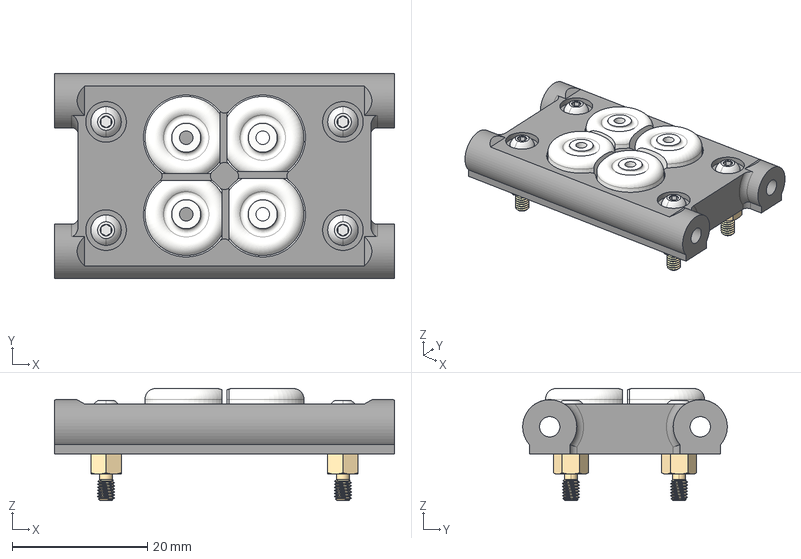
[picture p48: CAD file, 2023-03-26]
models/03_sub_assemblies/dragon_nose.step
50.2 x 30.2 x 16.6 mm
dragon_nose_1
95495K678_Adhesive-Back Bumpers x 4
92095A459_Button Head Hex Drive Screw x 4
93655A001_Male-Female Threaded Hex Standoff x 4

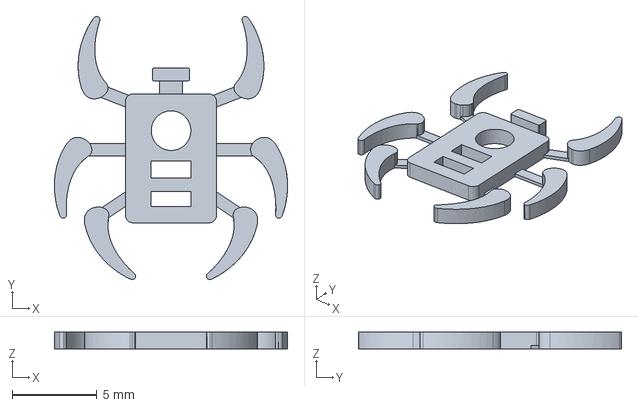
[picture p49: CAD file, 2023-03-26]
models/00_marks_and_decals/hexapod makers mark.step
13.7 x 15.5 x 1.00 mm

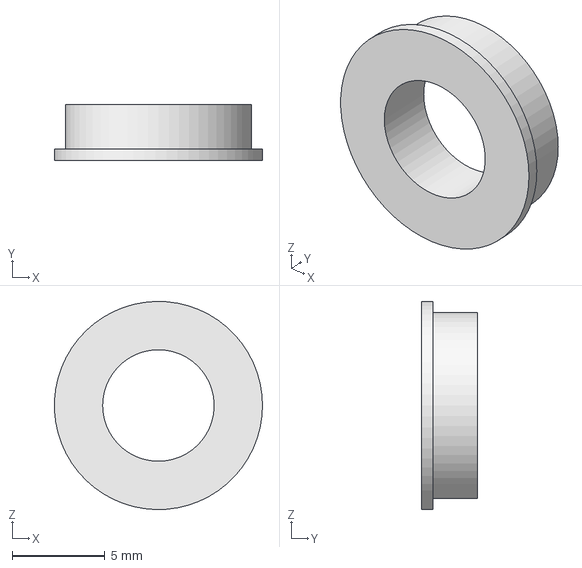
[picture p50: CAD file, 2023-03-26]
models/01_parts_stock/MF106ZZ.step
11.2 x 3.00 x 11.2 mm

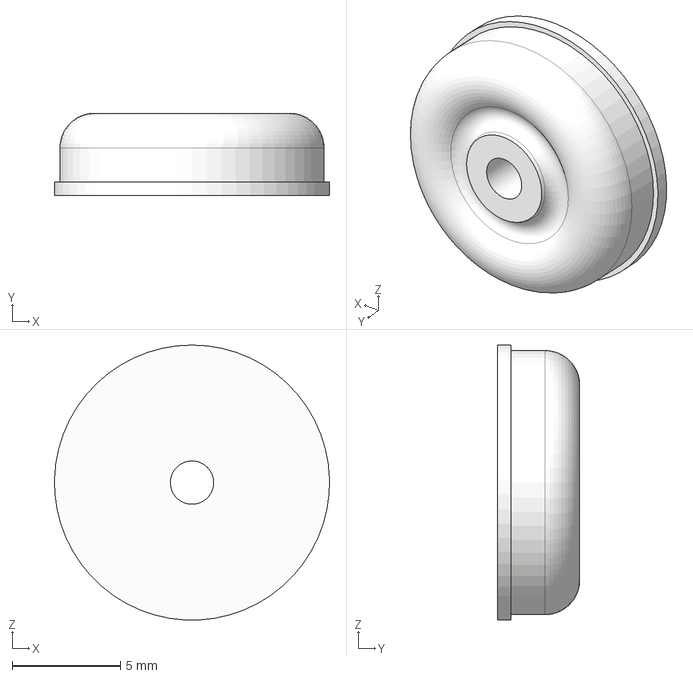
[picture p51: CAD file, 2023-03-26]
models/02_parts_custom/process_adhoc/iso_mount_A.step
12.7 x 3.81 x 12.7 mm

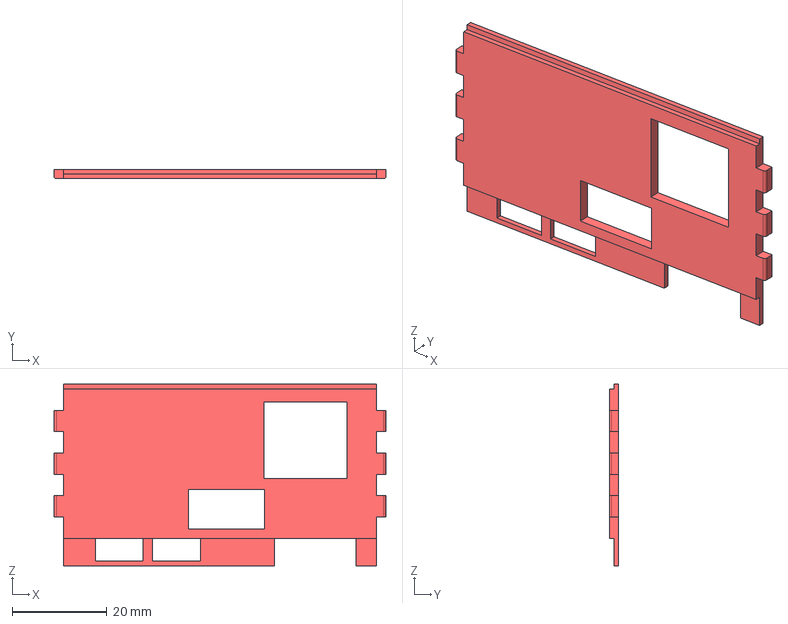
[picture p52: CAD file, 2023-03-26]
models/02_parts_custom/process_fff/dragon_beard_dust_cover_port.step
70.0 x 2.00 x 38.3 mm

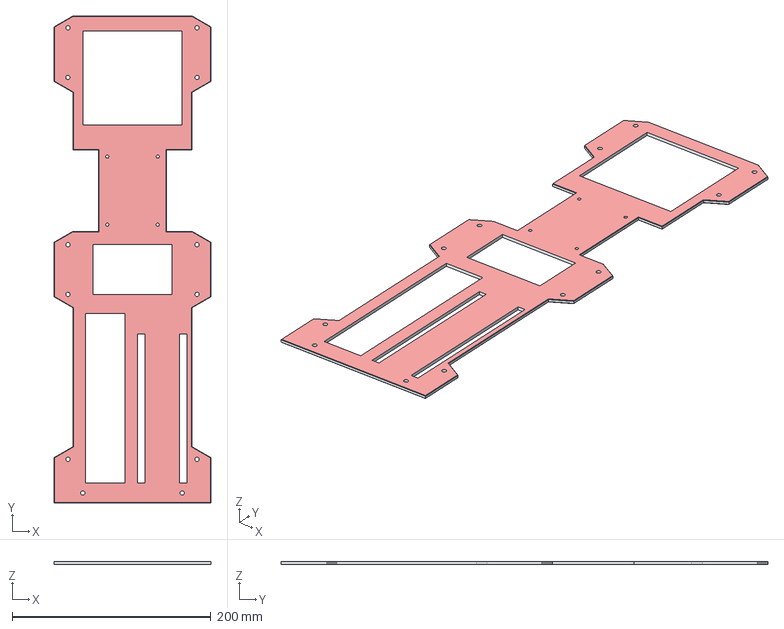
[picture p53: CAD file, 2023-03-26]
models/02_parts_custom/process_laser_cut/top-bracket.step
158.0 x 490.2 x 3.00 mm

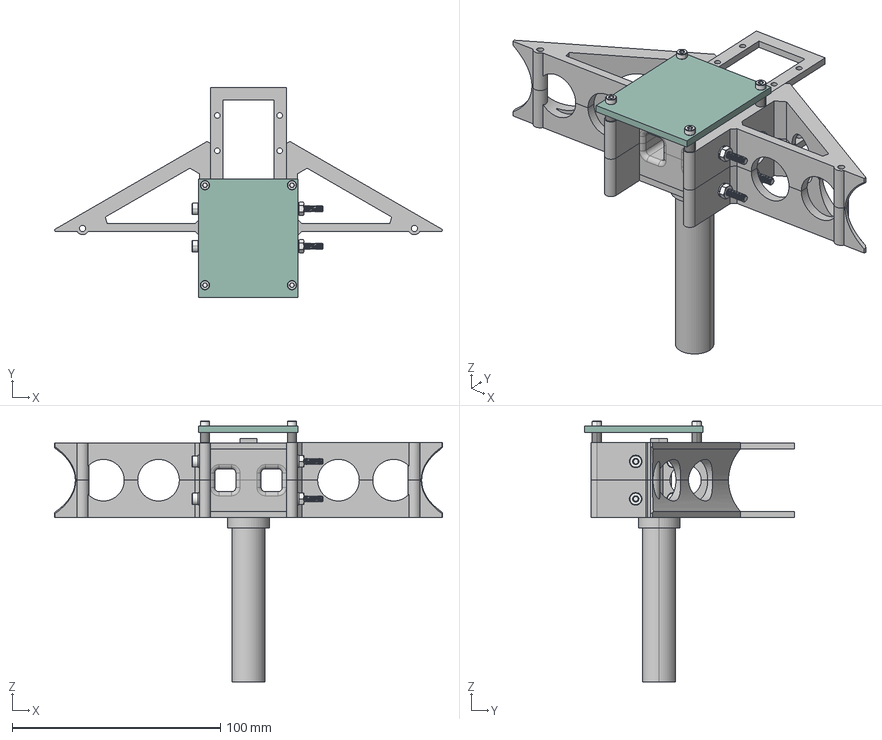
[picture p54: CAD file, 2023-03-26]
models/03_sub_assemblies/jig_teststand.step
186.5 x 101.1 x 125.5 mm
jig_teststand_dynamixel_bracket x 2
jig_teststand_post x 2
jig_teststand_bumper x 2
jig_teststand_dynamixel_bracket_spacer x 2
98689A112_General Purpose 18-8 Stainless Steel Washer x 8
91828A211_18-8 Stainless Steel Hex Nut x 4
91292A267_18-8 Stainless Steel Socket Head Screw x 4
U2D3PHB
99072A109_Black Nylon Unthreaded Spacer x 4
91292A018_18-8 Stainless Steel Socket Head Screw x 4

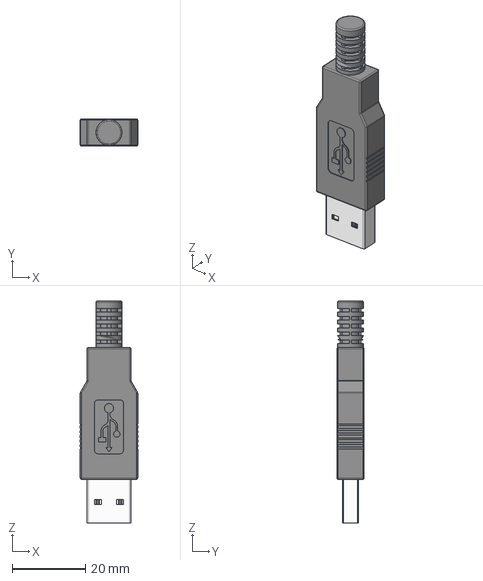
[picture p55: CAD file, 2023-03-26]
models/01_parts_stock/USB-A.step
15.7 x 7.49 x 60.6 mm

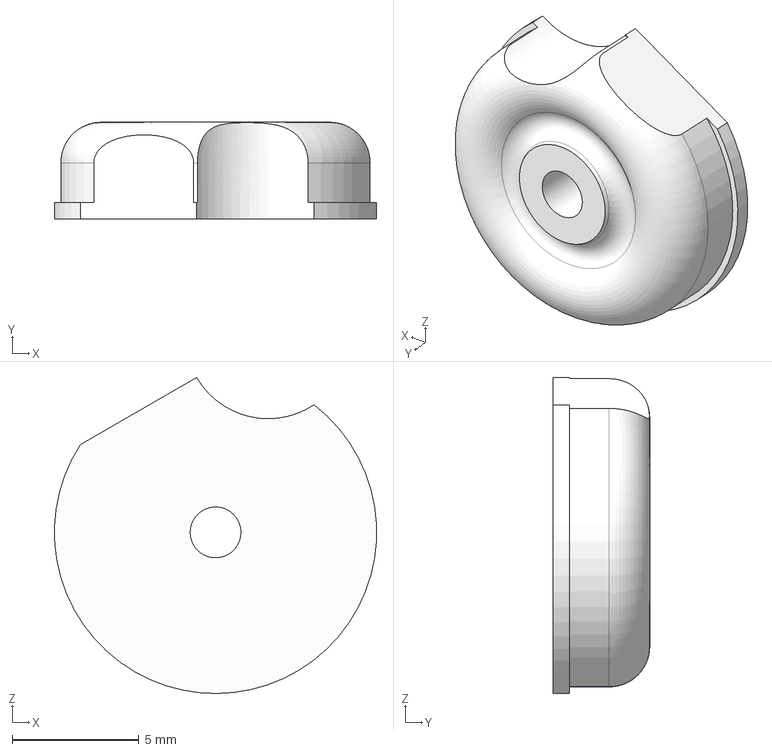
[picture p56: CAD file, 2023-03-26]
models/02_parts_custom/process_adhoc/iso_mount_C.step
12.7 x 3.81 x 12.5 mm

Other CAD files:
models/04_assemblies/AS1336.step
models/04_assemblies/AS1335.step
models/02_parts_custom/process_fff/dragon_neck_ethernet_guide_top.step
models/02_parts_custom/process_laser_cut/front-bracket.step
models/00_marks_and_decals/32 makers mark.f3d
models/00_marks_and_decals/hexapod makers mark.f3d
models/01_parts_stock/AAOTOKK USB A Micro 90 degree.f3d
models/01_parts_stock/AAOTOKK USB A Micro 90 degree.step
models/01_parts_stock/Adafruit Pi Zero Bonnet.f3d
models/01_parts_stock/FR07-B101.f3d
models/01_parts_stock/FR07-B101.step
models/01_parts_stock/FR07-H101-w-fasteners.f3d
models/01_parts_stock/FR07-H101-w-fasteners.step
models/01_parts_stock/FR07-H101.f3d
models/01_parts_stock/FR07-H101.step
models/01_parts_stock/FR07-S101-w-fasteners.f3d
models/01_parts_stock/Gigabit Ethernet Port, RPi4ModelB.f3d
models/01_parts_stock/Gigabit Ethernet Port, RPi4ModelB.step
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

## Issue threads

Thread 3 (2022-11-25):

[Feature Request] Design for new pan/tilt head

aentinger, 2022-11-25:
<a href="https://107-systems.org/">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</a>

### ⚡ Feature Request

For vision L3X-Z uses a pan/tilt head consisting of two Dynamixel MX-28AR with 2 x OpenMV [OpenMV Cam H7 R2](https://openmv.io/collections/cams/products/openmv-cam-h7-r2) cameras, one of those with a FLIR Lepton for thermal vision instead.

<p align="center">
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</a>
</p>

The [camera holder](https://github.com/107-systems/l3xz-hw/blob/main/cad/pan_tilt_head/cam_holder.FCStd) is a simple 3D printed part which is mouted on the Dynamixel MX-28AR servo via screws/nuts.

<p align="center">
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</a>
</p>

All design files are contained within [`cad/pan_tilt_head`](https://github.com/107-systems/l3xz-hw/tree/main/cad/pan_tilt_head).

**Please Describe The Problem To Be Solved**

In order to reduce cabling and processing requirements on the robots main control computer a [Raspberry Pi Zero 2W](https://www.raspberrypi.com/products/raspberry-pi-zero-2-w/) stacked with [Waveshare PoE/USB HAT](https://www.waveshare.com/poe-eth-usb-hub-hat.htm) will be mounted directly on the sensor head. The cameras will directly be connected to the USB Hub part of the HAT while the HAT itself will be connected to L3X-Zs PoE switch. Both communication and power will be supplied via the Ethernet connection - only a single cable connecting the robots head with the body will be necessary.

Therefore there's the need to design (or several) 3D printed parts allowing sensible mounting of both cameras as well as the computer/connectivity stack onto the back of the tilt Dynamixel MX-28AR servo.

aentinger, 2023-03-26:
Closed via #4.

Closed 2023-03-27.

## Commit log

2023-01-28 adding design files
    [00_main_v21.f3d, 00_main_v21.step, 32 makers mark_v1.f3d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]
2023-02-05 removing model files with version names
    [00_main_v21.f3d, 00_main_v21.step, 32 makers mark_v1.f3d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]
2023-02-05 adding model files without version
    [00_main.f3d, 00_main.step, 32 makers mark.f3d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]
2023-02-12 Start of build documentation.
    [jig_dragon_eye_truss_port.f3d, jig_dragon_eye_truss_port.step, jig_dragon_eye_truss_starboard.f3d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]
2023-02-12 adding ethernet guide assembly
2023-02-12 progress on BOM
2023-02-19 adding nose print
2023-03-05 Start on the dragon face assembly instructions
2023-03-12 adding more assemblies
2023-03-13 post-assembly notes for AS1334
2023-03-18 final definition of assemblies
2023-03-18 final dump of model
    [00_main.f3d, 00_main.step, 32 makers mark.f3d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]
2023-03-25 updates to assembly notes
2023-03-26 Insert missing space/removing superfluous space.

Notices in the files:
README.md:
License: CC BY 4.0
